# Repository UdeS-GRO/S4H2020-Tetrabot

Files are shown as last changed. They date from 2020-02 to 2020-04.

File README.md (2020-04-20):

# Tetrabot

Tetrabot is a four-legged robot made out of wooden parts with 8 DOF (2 per leg) that draws inspiration from Boston Dynamics' Spot. The motors are controlled with an Adafruit servo driver and both the walking cycle and the UI are coded in Python on a Raspberry PI 3.

ezgif com-optimize (1)

## Getting Started

Here, you'll find documentation on the CAD and the code used to create this robot as well as instructions to assemble it and to set up the coding environment.
The Tetrabot Mechanical Team (TMT) designed two prototypes. The first prototype has been fully tested and is made primarily of wood. The second prototype is made primarily of 3D printed PLA. Each part can be printed but it was not fully assembled and tested with the electronics and the software.

### FIRST Prototype Prerequisites (hardware)

Before setting up the coding environment, you should make sure you have the following to build the robot:

```
Machines and tools:
  - A laser cutter
  - A 3D printer
  - Pliers
  - Cutters
Materials:
  - 1/8" thick wood planks
  - Wood glue
  - C7: Sandpaper
Electronics:
  - C1: 1 Raspberry PI 3
  - C2: 8 Hitec HS-422 Servo Motor
  - C3: 1 Adafruit PCA9685 16-Channel Servo Driver
  - C4: 5 V - 3.2 A power supply
  - C5: 4 Long female to female electrical wires
  - C6: 2 Crocodile clips with wires
Others:
  - Nuts and bolts of various sizes
```

The laser cutter should be used to cut the following parts out of the wood plank:

```
  - A1 : 1 top (optionnal) (CAD->Top)
  - A2 : 1 bottom (CAD->Body)
  - A3 : 2 sides (left/right) (CAD->Mur)
  - A4 : 2 other sides (front/back) (CAD->face)
  - A5 : 4 thighs (CAD->thight)
  - A6 : 4 tibias (CAD->tibia)
```

And the 3D printer should be used to print the following parts with PLA plastic.

```
  - B1 : 8 custom servo horns (CAD->Adapteur_servo_metal)
  - B2 : 4 feet (CAD->New Tetrabot->foot)
```

### FIRST Prototype Assembling

A step by step guide to building the robot. Make sure you have all of the parts mentioned above before beginning the assembly.

1. Glue the body

```
  1.1. Apply some glue to the indents of the bottom (A2) and the sides (A3 and A4).
  1.2. Assemble the parts and use pliers to keep the parts together.
  1.3. Let the assembly dry.
```

2. Assemble the legs

```
  2.2. Screw the servo horns (B1) to the thighs (A5).
  2.3. Screw the motors (C2) to the thighs (A5).
  2.4. Screw the servo horns (B1) to the tibias (A6).
  2.5. Cut squares of sandpaper (C7) and glue them under the feet (B2).
  2.6. Screw the feet (B2) to the tibias (A6).
  2.7. Fix the tibias' servo horns to the thighs' motors.
```

3. Assemble the robot

```
  3.1. Once the base is dry, screw the remaining servos (C2) to the sides from the inside of the base.
  3.2. Fix the thighs' servo horns to the base's motors.
```

4. Setup the electronics

    You should follow the [adafruit tutorial](https://learn.adafruit.com/16-channel-pwm-servo-driver?view=all) to know how to setup the electronics.

```
  4.1. Weld the pins to the Adafruit driver (C3).
  4.2. Connect every servo wire to the driver like shown.
  4.3. Connect the driver (C3) to the PI using wires (C4) like shown.
  4.4. Connect the PI (C1) to a power source
  4.5. Plug in a keyboard and a mouse in the USB ports and a monitor in the HDMI port.
  4.6. Use wires to connect the Adafruit servo driver to a 5 V power supply.
```

5. After the software setup

```
  5.1. Unplug the monitor, screen, and mouse.
  5.2. Install (Don't glue!) the top of the robot. (If you have one)
```
### SECOND Prototype Prerequisites (hardware)

Every CAD that you need to make the final prototype is in the New Tetrabot folder. You will need these:

```
Machines and tools:
  - A 3D printer
  - Pliers
  - Cutters
Materials:
  - A7: Sandpaper
Electronics:
  - A1: 1 Raspberry PI 3
  - A2: 8 Hitec HS-422 Servo Motor
  - A3: 1 Adafruit PCA9685 16-Channel Servo Driver
  - A4: 5 V - 3.2 A power supply
  - A5: 4 Long female to female electrical wires
  - A6: 2 Crocodile clips with wires
Others:
  - Nuts and bolts of various sizes
```

The 3D printer should be used to print the following parts with PLA plastic. We used a MakerBot replicator+.

```
  - B1 : 1 base (CAD->New Tetrabot->Base2.01)
  - B2 : 4 feet (CAD->New Tetrabot->foot)
  - B3 : 4 whole thight (CAD->New Tetrabot->New_thigh_2)
  - B4 : 4 pierced thight (CAD->New Tetrabot->New_thigh)
  - B5 : 4 tibia (CAD->New Tetrabot->New_tibia)
  - B6 : 4 adapter (CAD->New Tetrabot->New_adapter)
```
The tibia and adapter should be printed with support with the part going in the motors facing up. The base, thigh and feet can be printed without support.

### SECOND Prototype Assembling

A step by step guide to building the robot. Make sure you have all of the parts mentioned above before beginning the assembly.

1. Assemble the legs

```
  1.1. Assemble and screw the two thighs (B3-B4) together with the adapter (B6) in the middle.
  1.2. Cut squares of sandpaper (A7) and glue them under the feet (B2).
  1.3. Screw the feet (B2) to the tibias (B5).
  1.4. Insert the tibias (B5) between the thighs.
  1.5. Screw the motors (A2) to the thighs (B4) while making sure that the motors are inserted in the tibias (B5).
```

2. Assemble the robot (some parts might collide, it was not fully tested)

```
  2.1. Insert the legs in the base (B1).
  2.2. Screw the motors (A2) to the base (B1) while making sure that the motors are in the thighs.
```

3. Setup the electronics

    You should follow the [adafruit tutorial](https://learn.adafruit.com/16-channel-pwm-servo-driver?view=all) to know how to setup the electronics.

```
  3.1. Weld the pins to the Adafruit driver (A3).
  3.2. Connect every servo wire to the driver like shown.
  3.3. Connect the driver (A3) to the PI using wires (A4) like shown.
  3.4. Screw the driver (A3) to the base (B1).
  3.5. Connect the PI (A1) to a power source.
  3.6. Plug in a keyboard and a mouse in the USB ports and a monitor in the HDMI port.
  3.7. Use wires to connect the Adafruit servo driver to a 5 V power supply.
```

### Prerequisites (software)

The tutorials that follow will state what you need to install their respective software.

### Installing

Follow this guide to install
[CircuitPython](https://learn.adafruit.com/circuitpython-on-raspberrypi-linux) on your Pi.

Follow [this guide](https://learn.adafruit.com/circuitpython-on-raspberrypi-linux) to setup your RaspberryPi with the
[Adafruit 16 Channel Servo Driver](https://learn.adafruit.com/16-channel-pwm-servo-driver?view=all).

Connect the servos to the drive:

```
Follow step 3 of the assembling tutorial above.
```

Once everything is set up, run `python3 servo.py` to make Tetrabot stand up.

You will need to change the `offset` values in `servo.py` until its legs are straight and perpendicular to the ground.

```
off_haut_gauche = [?, ?]
off_bas_gauche = [?, ?]
off_haut_droite = [?, ?]
off_bas_droite = [?, ?]

offset = [off_haut_gauche, off_haut_droite, off_bas_gauche, off_haut_gauche]
```

_Once the legs are straight, the setup is finished._

Run `python3 main.py` to start **Tetrabot**.

## Authors

- **Mathis Gagnon** - _Initial work_ - [MathisGagnon](https://github.com/mathisgag)
- **Alexandre Lafleur** - _Initial work_ - [AlexandreLafleur](https://github.com/alexandrelafleur)
- **Tristan Roy** - _Initial work_ - [TristanRoy](https://github.com/Tristan-01)
- **Félix-Antoine Toussaint** - _Initial work_ - [FélixAntoineToussaint](https://github.com/FAT8888)
- **Alexis Tremblay-Lebel** - _Initial work_ - [AlexisTremblayLebel](https://github.com/AlexisTB)
- **Philippe Turcotte** - _Initial work_ - [PhilippeTurcotte](https://github.com/turcottep)

## License

This project is licensed under the MIT License - see the [LICENSE.md](LICENSE.md) file for details

## Acknowledgments

- ZenHub Agile Project Management
- Authors of the CircuitPython and Adafruit tutorials
- Boston Dynamics' Spot
- PurpleBooth README.md template

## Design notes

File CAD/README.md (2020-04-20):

# CAD's

# DIRECTLY IN THIS FOLDER
CAD's of the first prototype.

To cut in wood:

```
Body.SLDPRT : Bottom plate of the body.
Face.SLDPRT : The face and rear of the body.
Mur.SLDPRT : Sides of the body.
thigh.SLDPRT : The thigh of the legs.
tibia.SLDPRT : The tibia of the legs.
Top.SLDPRT : The top plate of the body.
```

To print in PLA:

```
adapteur_servo_metal.SLDRPT : Custom servo horns that attach from the servos to the parts of the leg.
foot.SLDRPT : The foot of the leg. (in New Tetrabot)
```

To use as reference :

```
hs-422_horn_4wings_sws.SLDPRT : Default horn that attach to the servos
Leg.SLDASM : Full assembly of a leg
MiniBreadboard.SLDPRT : Breadboard
moteur.SLDPRT : Servo motor
Tetrabot.SLDASM : The full assembly of the first prototype
```

# IN New Tetrabot FOLDER
CAD's to use to build the final prototype

The tibia and adapter should be printed with support with the part going in the motors facing up. The base, thigh and feet can be printed without support.
To print in PLA:

```
Base2.01.sldprt : Full base.
foot.SLDPRT : The foot of the leg.
New_adapteur.SLDPRT : Horn that goes on the thigh servo.
New_Leg.SLDPRT : Full legs.
New_thigh.SLDPRT : Side of the thigh.
New_thigh_2.SLDPRT : Other side of the thigh.
New_tibia.SLDPRT : Tibia of the leg.
```

To use as reference :

```
moteur.SLDPRT : Servo Motor
jambe.SLDASM : Full thigh.
New_Tetrabot.SLDASM : Full assembly of the robot.
Raspberry Pi 3 Light Version.SLDPRT : Raspberry Pi.
```

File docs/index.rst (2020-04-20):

.. Tetrabot documentation master file, created by
   sphinx-quickstart on Thu Apr 16 14:58:14 2020.
   You can adapt this file completely to your liking, but it should at least
   contain the root `toctree` directive.

Welcome to Tetrabot's documentation!
====================================

.. automodule:: main
   :members:

.. automodule:: gui
   :members:

.. automodule:: display
   :members:

.. automodule:: inverse_kinematics
   :members:

.. automodule:: positions
   :members:

.. automodule:: servo
   :members:

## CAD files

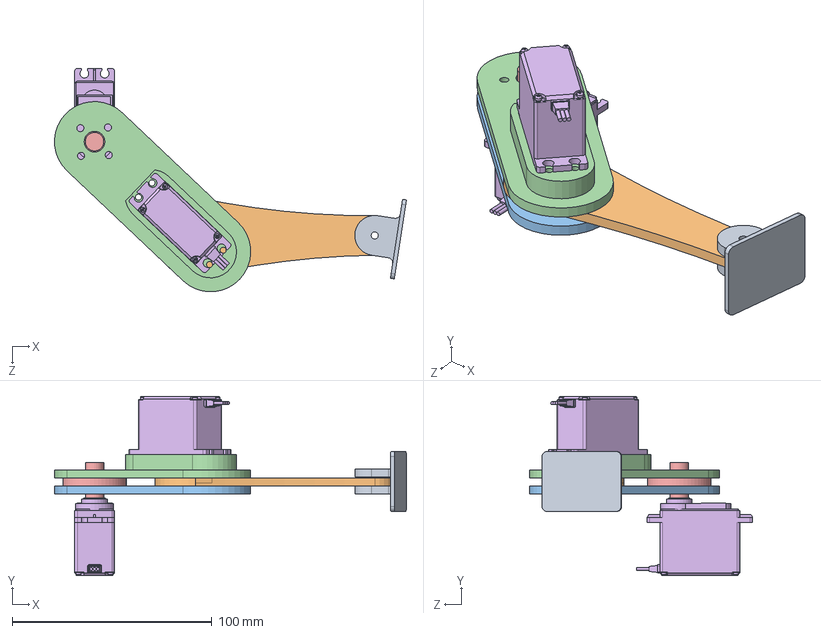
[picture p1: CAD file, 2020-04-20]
CAD/New Tertrabot/New_Leg.SLDASM
176.1 x 89.8 x 111.8 mm
foot
New_tibia
New_thigh_2
New_thigh
New_adapter
moteur x 2

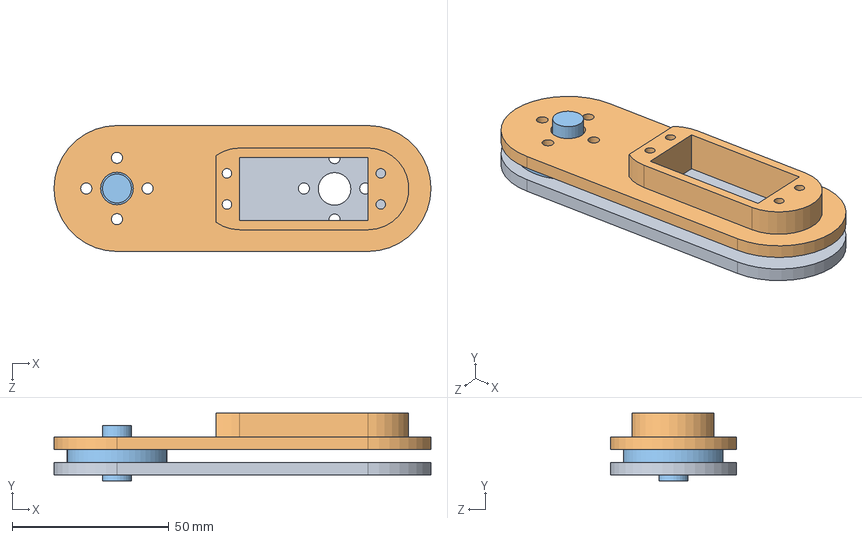
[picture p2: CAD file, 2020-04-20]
CAD/New Tertrabot/jambe.SLDASM
120.1 x 21.7 x 40.1 mm
New_thigh_2
New_thigh
New_adapter

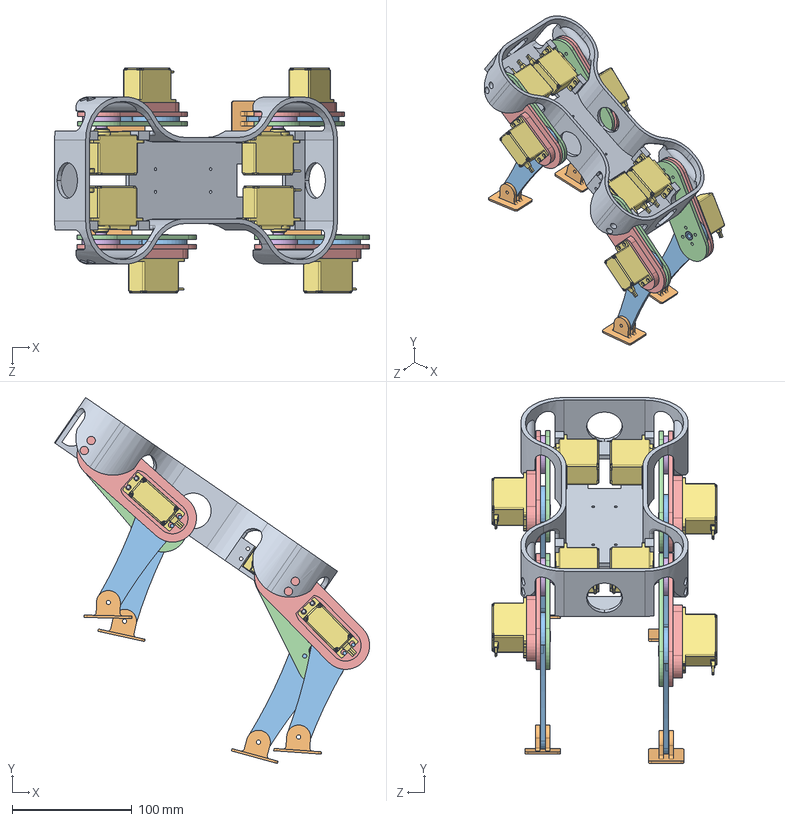
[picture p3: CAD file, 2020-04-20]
CAD/New Tertrabot/New_Tetrabot.SLDASM
263.7 x 306.2 x 188.6 mm
Base2.01
foot x 4
New_tibia x 4
New_thigh_2 x 4
New_thigh x 4
New_adapter x 4
moteur x 8

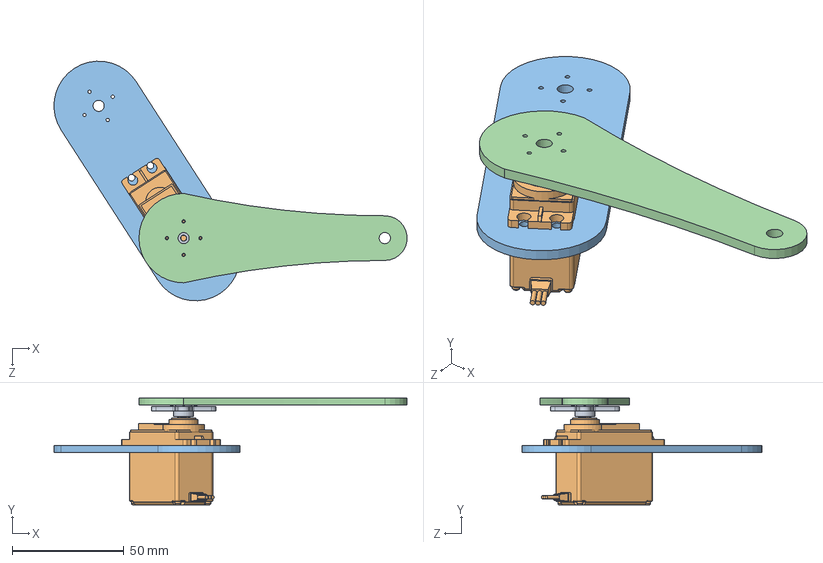
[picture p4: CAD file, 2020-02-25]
CAD/Leg.SLDASM
157.9 x 47.8 x 107.2 mm
hs-422_horn_4wings_sws
moteur
thigh
tibia

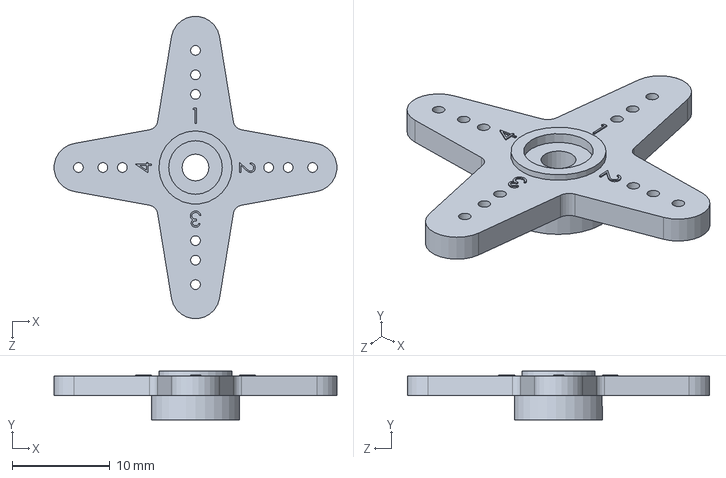
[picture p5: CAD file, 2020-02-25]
CAD/hs-422_horn_4wings_sws.SLDPRT
29.0 x 5.00 x 31.0 mm

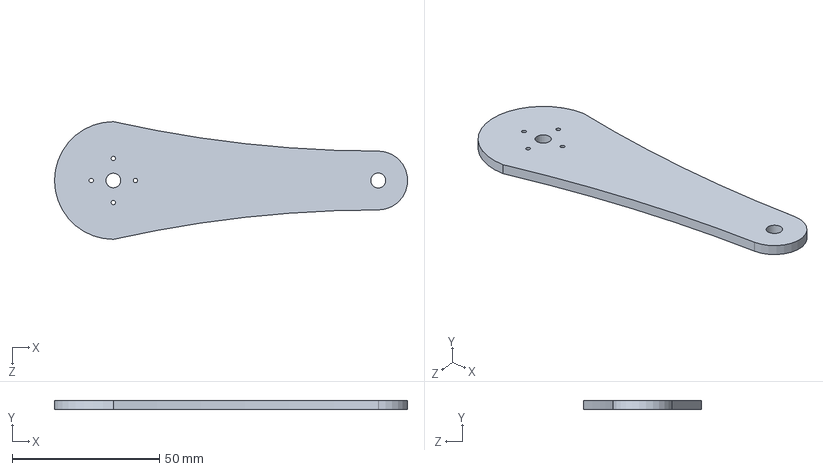
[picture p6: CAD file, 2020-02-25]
CAD/tibia.SLDPRT
119.9 x 3.17 x 40.0 mm

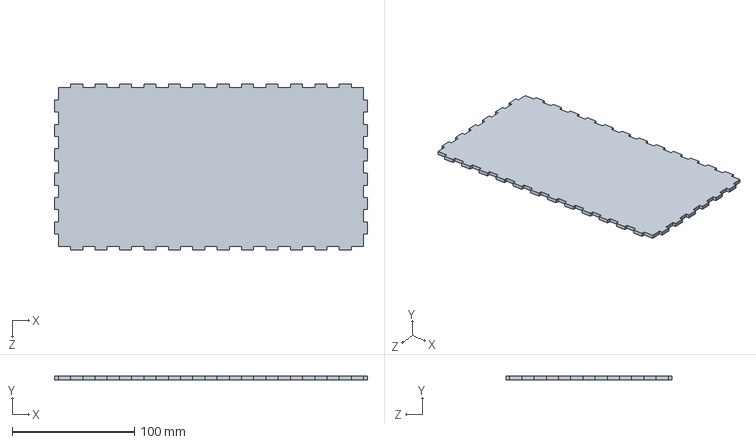
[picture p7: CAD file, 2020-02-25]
CAD/Body.SLDPRT
256.3 x 3.17 x 136.4 mm

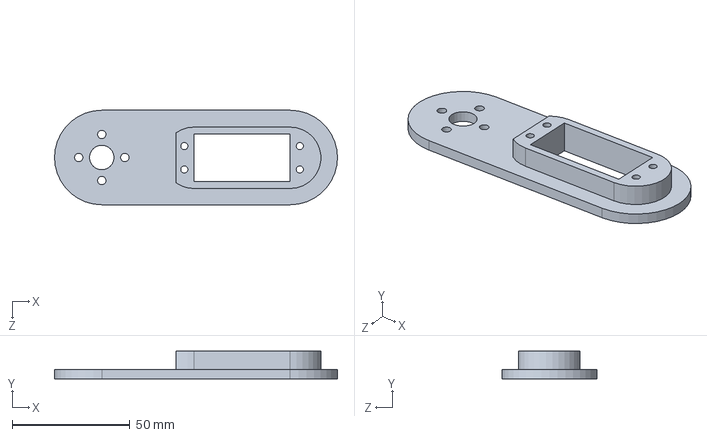
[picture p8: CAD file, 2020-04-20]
CAD/New Tertrabot/New_thigh.SLDPRT
120.1 x 11.7 x 40.1 mm

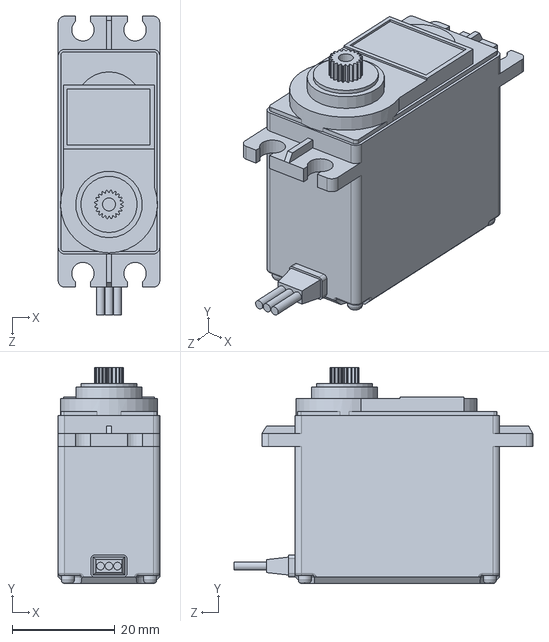
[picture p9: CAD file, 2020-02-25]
CAD/moteur.SLDPRT
19.8 x 42.1 x 58.2 mm

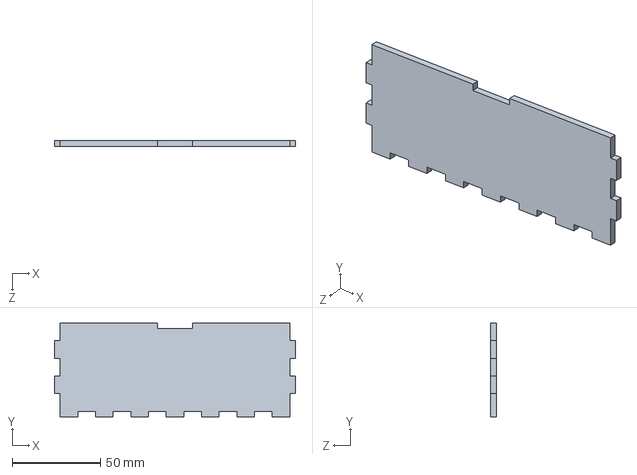
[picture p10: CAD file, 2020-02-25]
CAD/Face.SLDPRT
136.4 x 53.2 x 3.17 mm

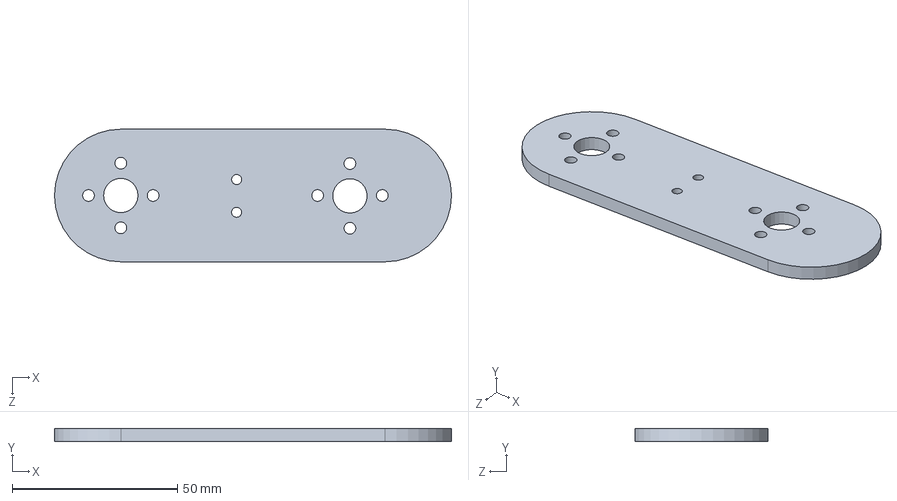
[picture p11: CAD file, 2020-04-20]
CAD/New Tertrabot/New_thigh_2.SLDPRT
120.1 x 4.00 x 40.1 mm

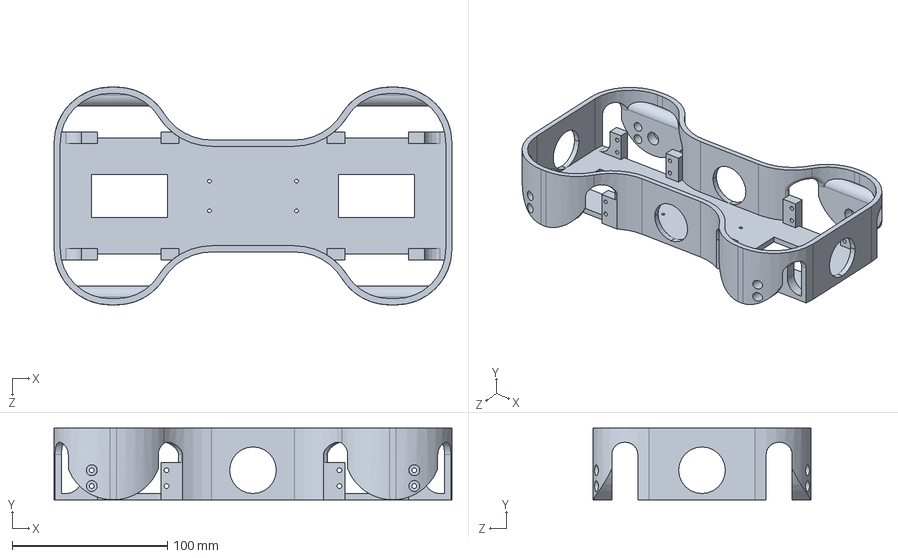
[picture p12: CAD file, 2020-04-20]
CAD/New Tertrabot/Base2.01.sldprt
256.0 x 46.0 x 140.0 mm

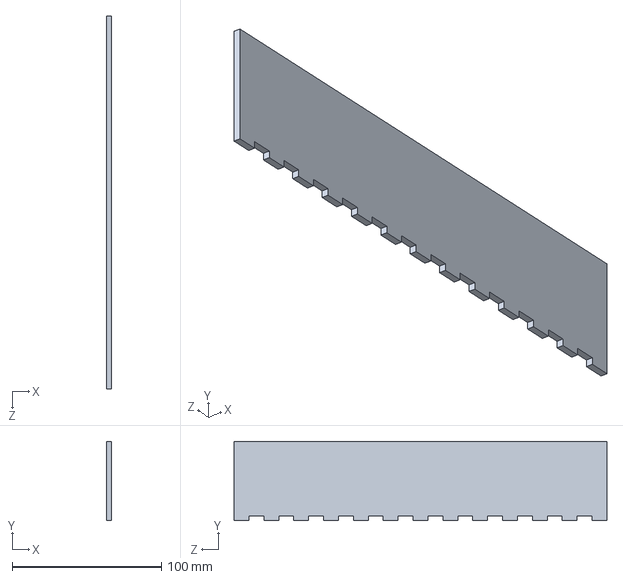
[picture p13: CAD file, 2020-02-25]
CAD/Pièce1.SLDPRT
3.17 x 53.2 x 250.0 mm

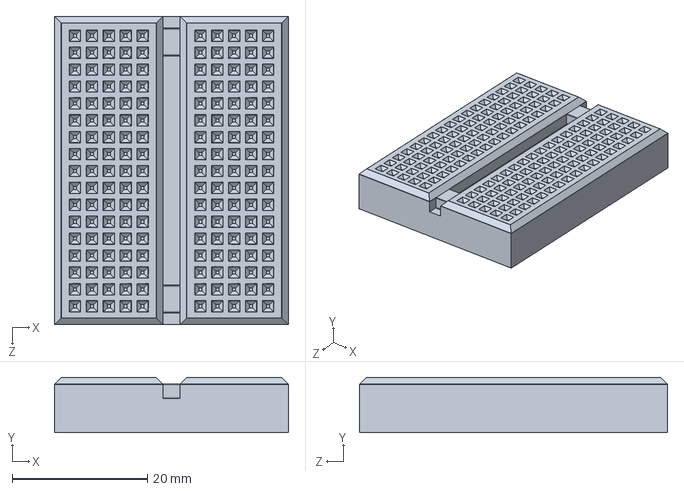
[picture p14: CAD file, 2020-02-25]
CAD/MiniBreadboard.SLDPRT
34.6 x 8.15 x 45.6 mm

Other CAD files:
CAD/New Tertrabot/foot.SLDPRT
CAD/New Tertrabot/New_tibia.SLDPRT
CAD/Top.SLDPRT
CAD/New Tertrabot/New_adapter.SLDPRT
CAD/Mur.SLDPRT
CAD/New Tertrabot/moteur.SLDPRT
CAD/Pièce9.SLDPRT
CAD/adaptateur_servo_metal.SLDPRT
CAD/foot.SLDPRT
CAD/thigh.SLDPRT

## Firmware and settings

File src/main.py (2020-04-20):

from src.gui import Gui
from src.positions import get_positions_from_walk_sequence, steps_smoother, get_angles_from_positions, stand_up_move


class Controler:
    """
    Class to control parameters of the walk sequence and simulation
    """

    def __init__(self):
        """
        :param step_index: the index of the current step in the simulation
        :param resolution: the resolution of the simulation
        :param period: the period of the resolution of the simulation
        :param delay: the pause between each walking sequence
        :param state: case in the switch case
        :param active_servo: the config with rasberry pi for the servos
        """

        self.step_index = 0
        self.resolution = 5
        self.period = 500
        self.delay = int(self.period / self.resolution)
        self.state = 0
        self.active_servo = 0

        # sets the steps to the desired walk sequence and the resolution
        self.steps = get_angles_from_positions(
            steps_smoother(stand_up_move(), self.resolution))

        # Inits the GUI for the animation view
        self.gui = Gui()

    # Main loop for the animations and walk sequence of the robot
    def main_loop(self):
        # Checks if the GUI is opened and running (for the simulation)
        stand_up = self.gui.var_standing.get()
        run = self.gui.var_running.get()

        if self.state == 0:  # Wait command stand_up
            if stand_up:
                if self.step_index >= len(self.steps)/2:
                    self.state = 1
                else:
                    self.step_index += 1

        elif self.state == 1:  # Stand_up and wait command run
            if run:
                self.step_index = 0
                self.steps = get_angles_from_positions(steps_smoother(
                    get_positions_from_walk_sequence(), self.resolution))
                self.state = 2

        elif self.state == 2:  # Run and wait futur command
            if run:
                if self.step_index + 1 >= len(self.steps):
                    self.step_index = 0
                else:
                    self.step_index += 1

        elif self.state == 3:  # Futur state
            pass

        if self.gui.var_servo_activation.get() and not self.active_servo:
            self.active_servo = 1
            from src.servo import init_servos, move as write_to_servos
            init_servos()

        step = self.steps[self.step_index]
        self.gui.animate_step(step)
        if self.active_servo:
            write_to_servos(step)
        self.gui.root.after(self.delay, self.main_loop)


# Runs the main_loop of the object "controler". (starts the GUI, starts the main_loop)
if __name__ == "__main__":
    controler = Controler()
    controler.main_loop()
    controler.gui.root.mainloop()

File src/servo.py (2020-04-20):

from adafruit_servokit import ServoKit
from math import pi


def rad_to_deg(rad):
    return rad*180/pi


kit = ServoKit(channels=16)

off_haut_gauche = [88, 155]
off_haut_droite = [94, 35]
off_bas_gauche = [89, 148]
off_bas_droite = [97, 8]

offset = [off_haut_gauche, off_haut_droite, off_bas_gauche, off_bas_droite]


def format_step_for_servo(step):
    formatted_step = []
    for leg_angles in step:
        angle0 = rad_to_deg(leg_angles[0])
        angle1 = rad_to_deg(leg_angles[1])
        formatted_step.append([angle0, angle1])

    return formatted_step


def init_servos():
    """
    Init the range of servos for the corrected pulse (in ms)
     """
    for i in range(0, 7):
        kit.servo[i].actuation_range = 180
        kit.servo[i].set_pulse_width_range(450, 2550)


def move(step):
    position = format_step_for_servo(step)
    """
     :param position: position array for each joint
     """
    # haut gauche
    kit.servo[0].angle = offset[0][0] + .9 * position[0][0]
    kit.servo[1].angle = offset[0][1] - .9 * position[0][1]
    # haut droite
    kit.servo[2].angle = offset[1][0] - .9 * position[1][0]
    kit.servo[3].angle = offset[1][1] + .9 * position[1][1]
    # bas gauche
    kit.servo[4].angle = offset[2][0] + .9 * position[2][0]
    kit.servo[5].angle = offset[2][1] - .9 * position[2][1]
    # bas droite
    kit.servo[6].angle = offset[3][0] - .9 * position[3][0]
    kit.servo[7].angle = offset[3][1] + 1.25 * position[3][1]


if __name__ == "__main__":
    init_servos()
    thet = -3*pi/4
    thet2 = pi/2
    move([[thet, thet2], [thet, thet2], [thet, thet2], [thet, thet2]])

    # offset_th_0 = [90,70,115,93]
    # offset_th_1 = [140,127,40,15]

    # kit.servo[0].angle = offset_th_0[0] + .9*thigh[0]
    # kit.servo[1].angle = offset_th_1[0] - .9*knee[0]

    # kit.servo[2].angle = offset_th_0[1] + .9*thigh[1]
    # kit.servo[3].angle = offset_th_1[1] - .9*knee[1]

    # kit.servo[4].angle = offset_th_0[2] - .9*thigh[2]
    # kit.servo[5].angle = offset_th_1[2] + .9*knee[2]

    # kit.servo[6].angle = offset_th_0[3] - .9*thigh[3]
    # kit.servo[7].angle = offset_th_1[3] + 1.25*knee[3]

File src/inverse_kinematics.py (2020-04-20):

import math


def inverse_kinematic(x, y, a1, a2):
    """
    :param x: x position of end effector
    :param y: y position of end effector
    :param a1: length of member 1
    :param a2: length of member 2

    :return: angles of a 2 joint same plane robot arm
    """
    # find q2 angle of the second joint
    num = x ** 2 + y ** 2 - a1 ** 2 - a2 ** 2
    denum = 2 * a1 * a2
    q2 = math.acos(num / denum)

    # find q1 angle of the first joint
    num = a2 * math.sin(q2)
    denum = a1 + a2 * math.cos(q2)
    epsilon = 0.000001
    q1 = math.atan(y / (x + epsilon)) - math.atan(num / (denum + epsilon))
    return q1, q2

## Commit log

2020-01-16 [TetraBot]: Adding Firmata support on arduino, and firmata code test in py
2020-01-16 [Tetrabot]: Added CAD folder
    [cuisse_tetrabot.SLDPRT]
2020-01-16 Add CAD of the adaptateur from a servo to a metal piece
    [adaptateur_servo_metal.SLDPRT]
2020-01-19 Widden the space for the cogs
    Change diameter of the extrusion from 0.354331 to 0.359331
    Change depth of the teeths from 0.118110 to 0.120110
    [adaptateur_servo_metal.SLDPRT]
2020-01-22 Widden space and add adaptateur_servo_bigger.STL
    Change diameter of the extrusion from 0.359331 to 0.364331
    Change depth of the teeths from 0.120110 to 0.122110
    [adaptateur_servo_bigger.STL, adaptateur_servo_metal.SLDPRT]
2020-01-22 [TetraBot]: Moving servomotors
2020-01-22 [TetraBot]: Update to servo control
2020-01-22 Complete CAD of legs
    [assembly.SLDASM, cuisse_tetrabot.SLDPRT, hs-422_horn_4wings_sws.SLDPRT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]
2020-01-22 Box CAD
    [ArduinoMega_STEP_AP203.STEP, Body.SLDPRT, Face.SLDPRT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]
2020-01-31 [TetraBot]: Adding leg files
    [hs-422_horn_4wings_sws.SLDPRT, moteur.SLDPRT, thigh.SLDPRT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]
2020-01-31 added 3d view of legs
2020-01-31 [TetraBot]: Removing all WIP from master
    [ArduinoMega_STEP_AP203.STEP, Body.SLDPRT, Face.SLDPRT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]
2020-02-05 Pack canvas and button
2020-02-05 [TetraBot]: Servos with python on raspberryPi
2020-02-17 first draft
    add the first draft of the final body.
    [Base2.0.SLDPRT]
2020-02-25 change base
    [Base2.0.SLDPRT]
2020-02-25 Removed old CAD and added new CAD
    [ArduinoMega_STEP_AP203.STEP, Base2.0.SLDPRT, Base2.0.step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]
2020-02-25 Added assembly
2020-03-10 changed vector base to allow leg backward movement
2020-03-11 Removing print
2020-03-11 add drive holes
    [Base2.01.sldprt]
2020-03-11 Main with switch case for different fonctions
    2020/03/11
2020-03-26 Change CAD to their print
    [Base2.01.sldprt, New_thigh.SLDPRT, New_thigh_2.SLDPRT]
2020-03-26 Add Adapteur
    [adaptateur_servo_metal.SLDPRT]
2020-03-26 Uodate documention on the mecanics
    [Base2.0.step]
2020-03-28 fix CAD readme
2020-04-01 Correction
    Repeatability of movement
    [main.py]
2020-04-06 Change New_Tetrabot.SLDASM
    Final CAD
    [Base2.01.sldprt, New_Leg.SLDASM, New_Tetrabot.SLDASM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]
2020-04-16 New readme
    [Base2.01.sldprt, New_Tetrabot.SLDASM]
2020-04-16 Ajoute des liens
    C'était pas clair
2020-04-17 Forget erase print
